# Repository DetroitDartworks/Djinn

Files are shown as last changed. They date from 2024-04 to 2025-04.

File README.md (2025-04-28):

*     05/22/24 - Updated Brushless Noidcore file(s) to fix some issues
*     06/13/24 - Added new Buttplate v2, Added new thumbhole stock extenders (must use Buttplate v1 with the extenders)
*     07/18/24 - Uploaded updated base flywheels (DDW Xing2 1404) AND new high concavity "Djinnshee" wheels for the Xing2 1404 motors
*     10/11/24 - Uploaded BETA Gonk-style PCAR insert for use with Djinnshee wheels, faux insert, and extended flycore dart guide
*     04/28/25 - Added new Board Box v2 that reinforces the upper portion of the Board Box for better retention. This can also still be used if the retention tab on the Lower breaks off

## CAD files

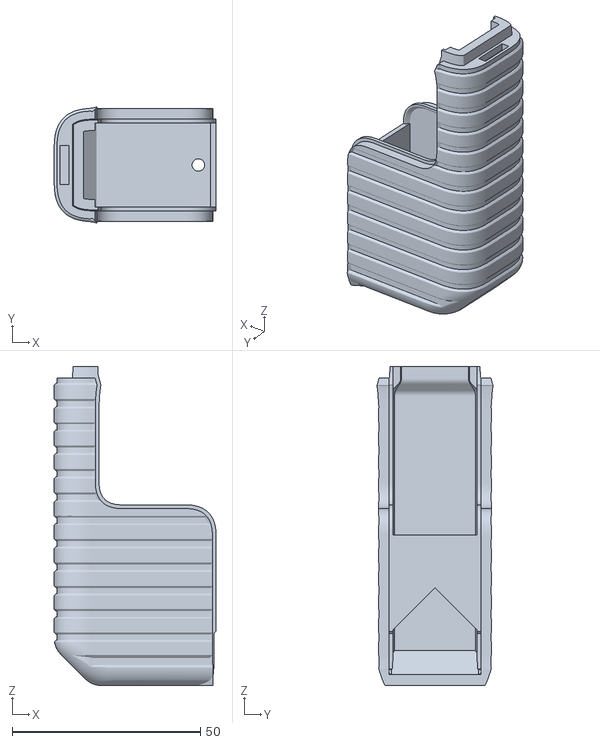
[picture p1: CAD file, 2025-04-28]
DDW Djinn - Board Box v2/DDW Djinn - Board Box v2.stl
42.9 x 30.9 x 84.6

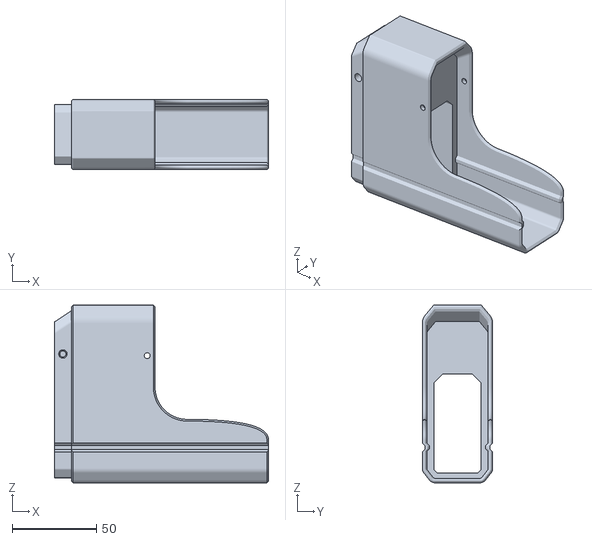
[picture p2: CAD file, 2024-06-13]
DDW Djinn Thumbhole Stock Extenders/DDW DJINN - Thumbhole Extender 50mm.stl
127.0 x 41.8 x 105.5

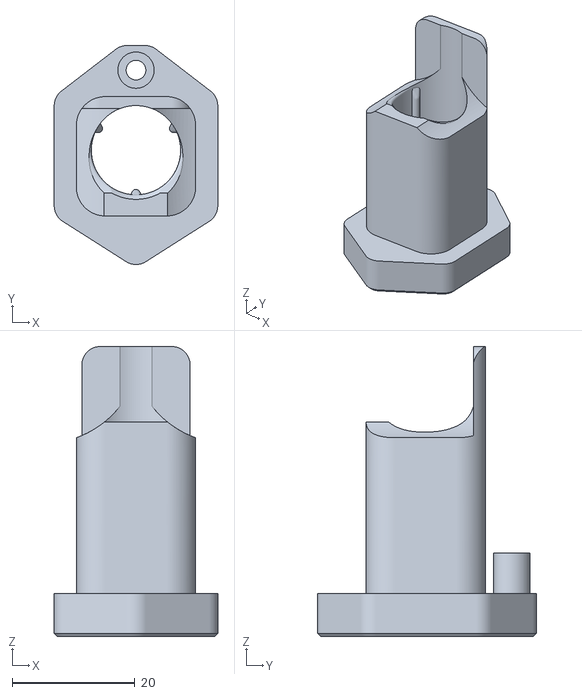
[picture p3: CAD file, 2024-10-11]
DDW Djinnshee Gonk PCAR Insert v3/DDW Djinnshee Gonk PCAR Insert v3.stl
26.6 x 35.6 x 47.2

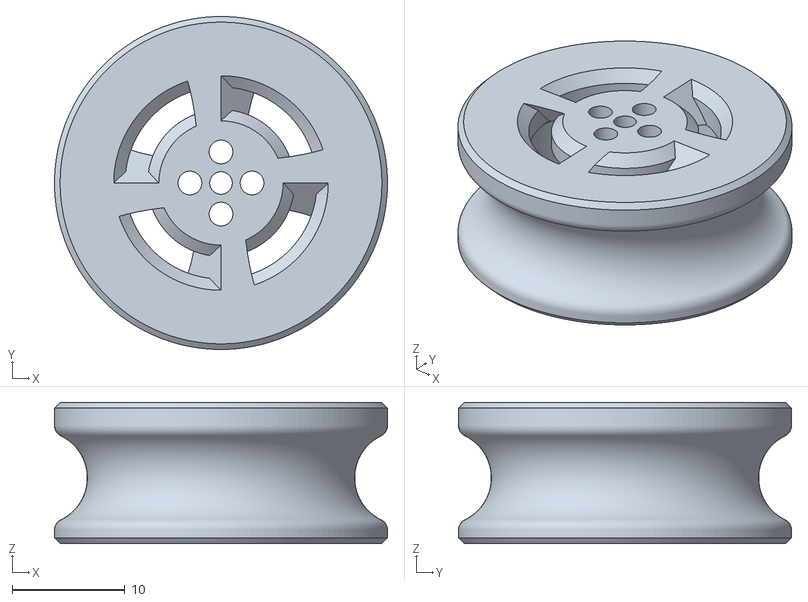
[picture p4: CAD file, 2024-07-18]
DDW Djinnshee Xing2 1404 Wheels/DDW Djinnshee Wheels Xing2 1404 v1 Mirror.stl
29.5 x 29.5 x 12.5

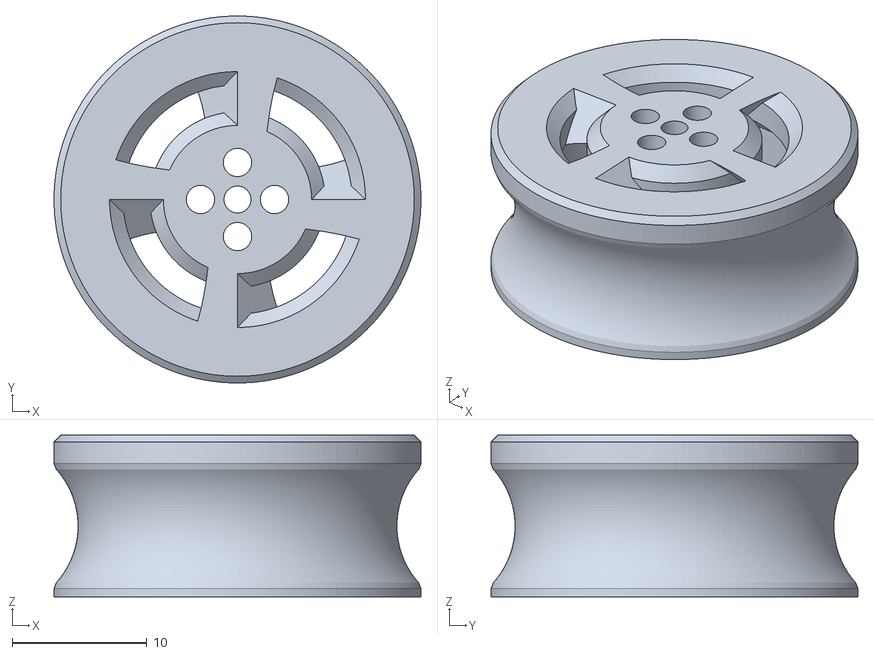
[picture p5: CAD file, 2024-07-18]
DDW Xing2 1404 Wheels and Dart Guide/Xing2 1404 DDW Wheel v4 Mirror.stl
27.2 x 27.2 x 12.0

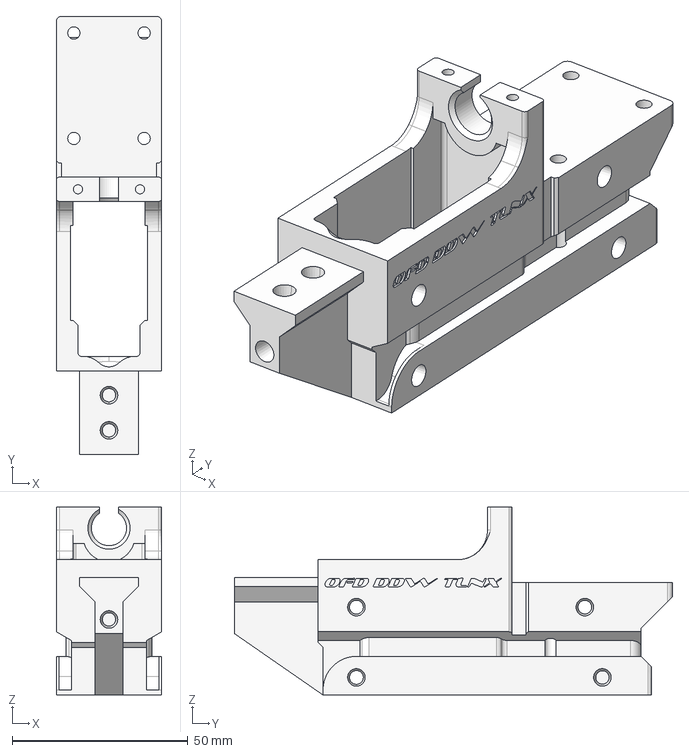
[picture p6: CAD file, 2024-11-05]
OFD-DDW-TLNX - BL NOIDCORE V2/OFD-DDW-TLNX BL NOIDCORE V2.step
30.0 x 124.8 x 53.5 mm

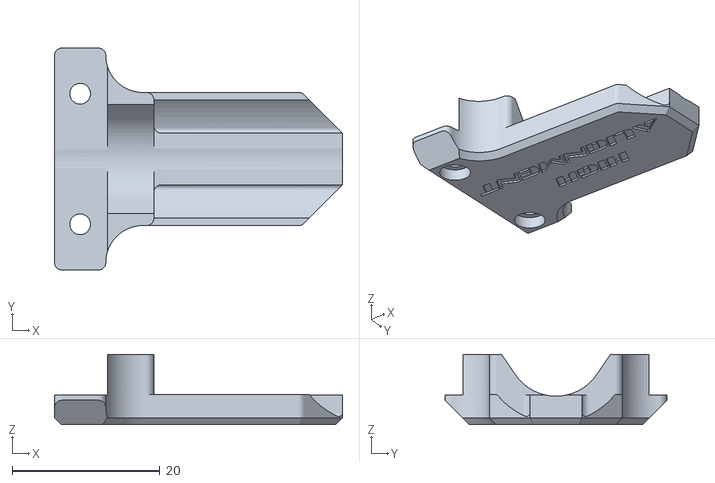
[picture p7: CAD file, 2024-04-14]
TalonaxeArmory_DDW_OFD_Modular_Brushless_Flycore/Dart Guides/NOIDCORE_Pusher_Guide_High_Straight_V1.STL
38.9 x 30.0 x 9.50

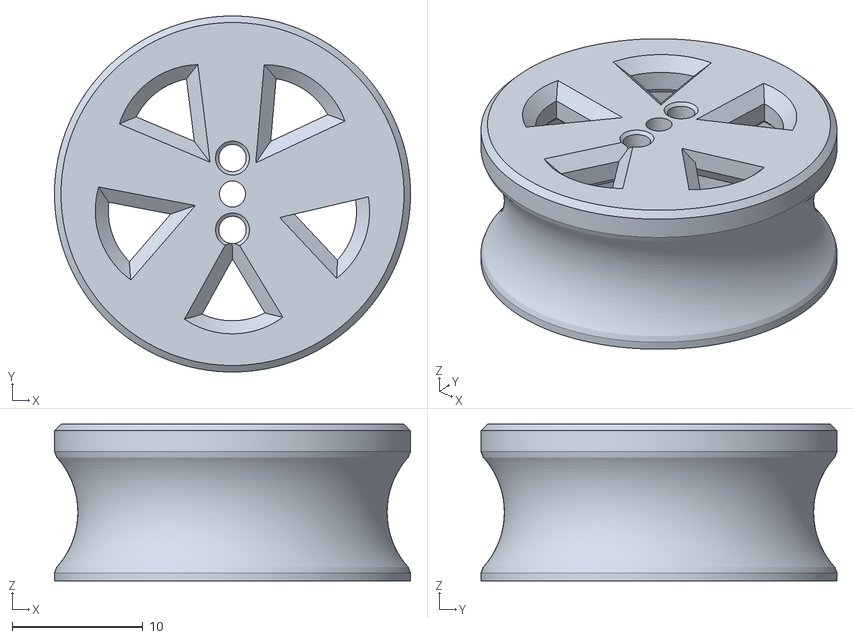
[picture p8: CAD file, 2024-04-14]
TalonaxeArmory_DDW_OFD_Modular_Brushless_Flycore/Flywheels/Xing2_1404Flywheel_v11.stl
27.2 x 27.2 x 12.0

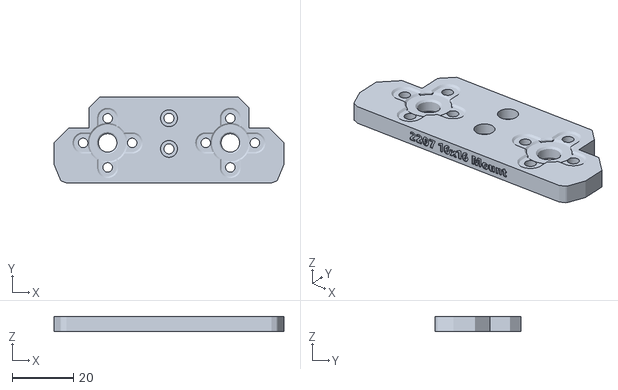
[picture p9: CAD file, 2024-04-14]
TalonaxeArmory_DDW_OFD_Modular_Brushless_Flycore/Motor Trays/2207Motors-40mmCrush-1616Mount_v2.stl
75.0 x 28.1 x 5.00

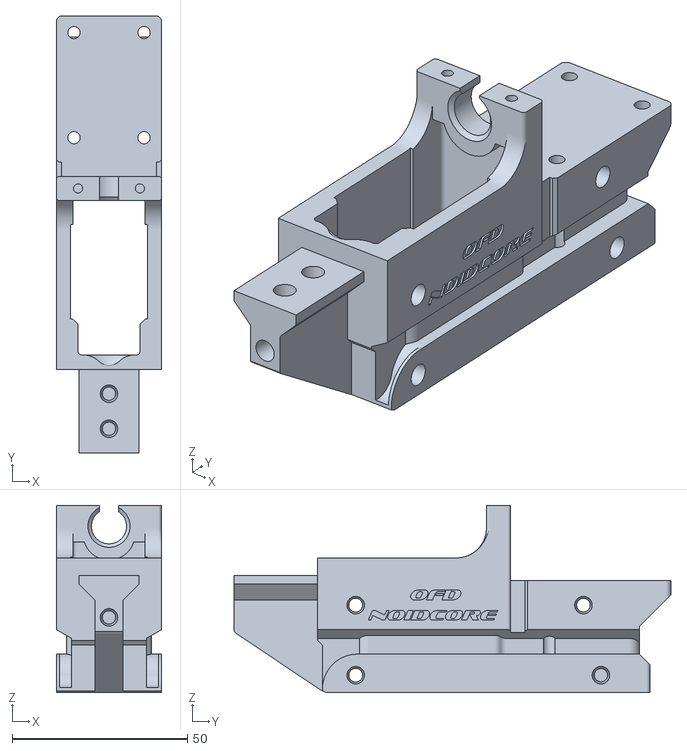
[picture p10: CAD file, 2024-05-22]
TalonaxeArmory_DDW_OFD_Modular_Brushless_Flycore/Talonaxe_DDW_OFD_Modular_Brushless_Flycore v12.stl
30.0 x 124.8 x 53.5

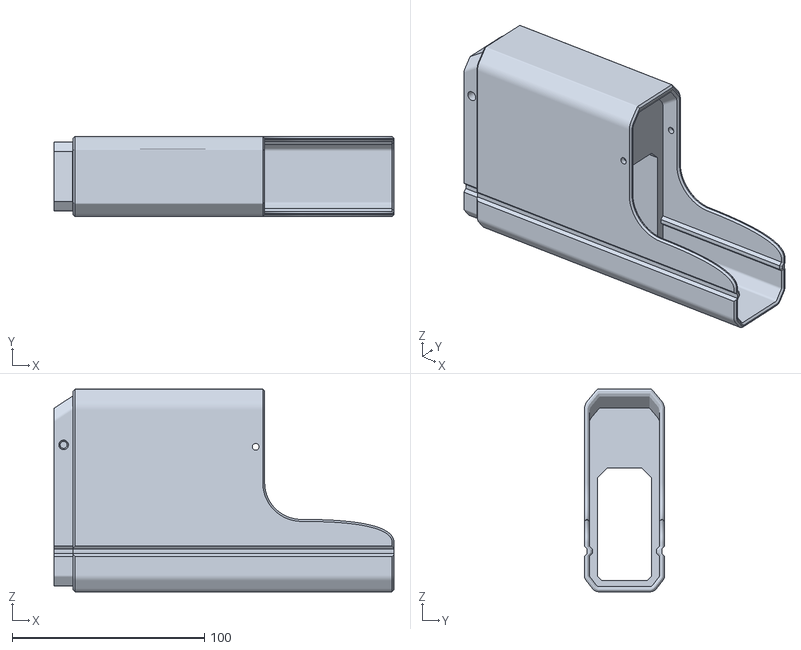
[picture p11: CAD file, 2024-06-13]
DDW Djinn Thumbhole Stock Extenders/DDW DJINN - Thumbhole Extender 100mm.stl
177.0 x 41.8 x 105.5

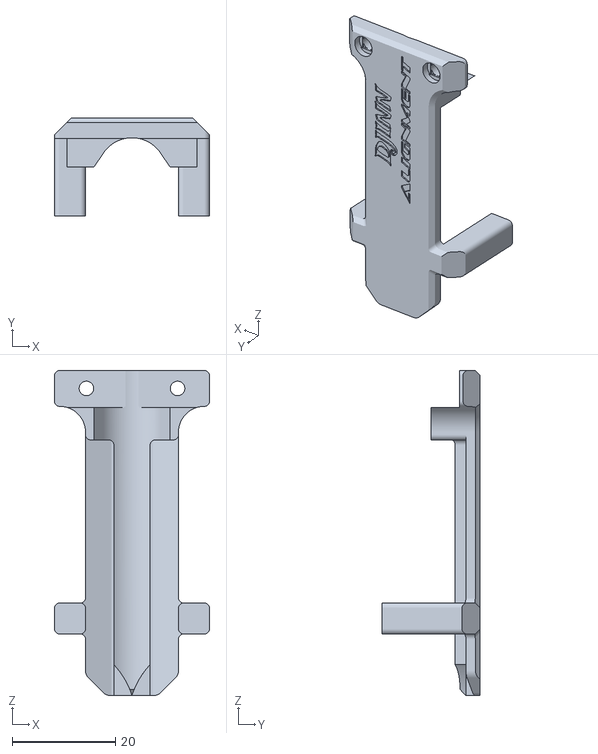
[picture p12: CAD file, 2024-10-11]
DDW Djinnshee Gonk PCAR Insert v3/Djinnshee Extended Pusher Guide.stl
30.0 x 19.0 x 62.9

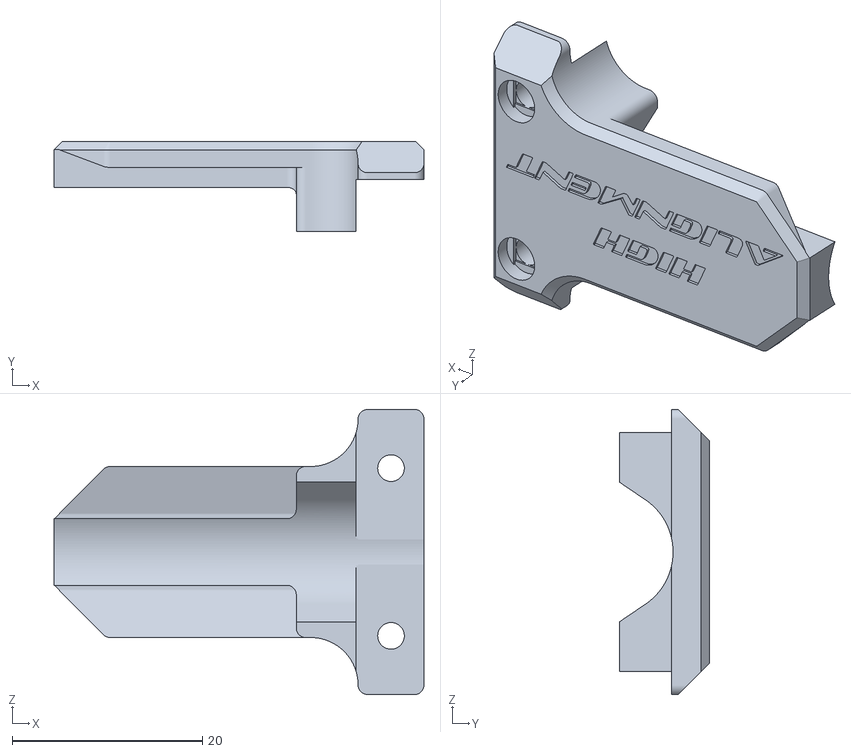
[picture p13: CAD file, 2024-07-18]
DDW Xing2 1404 Wheels and Dart Guide/Djinn Dart Guide.stl
38.9 x 9.50 x 30.0

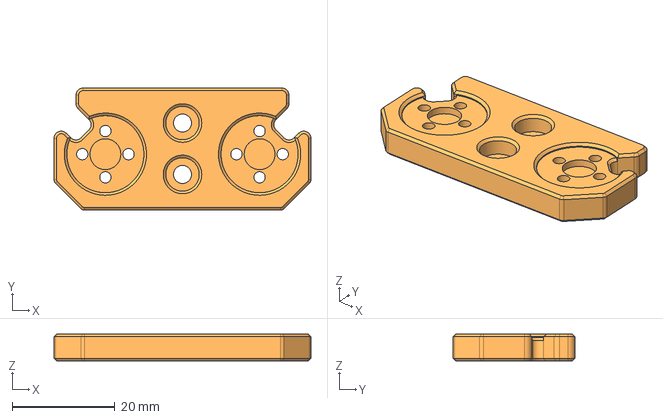
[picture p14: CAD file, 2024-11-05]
OFD-DDW-TLNX - BL NOIDCORE V2/MOTOR TRAY - OFD-DDW-TLNX BL NOIDCORE V2 - 30mm Xing2 1404.step
50.0 x 23.7 x 5.20 mm

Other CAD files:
DDW Djinnshee Xing2 1404 Wheels/DDW Djinnshee Wheels Xing2 1404 v1.stl
TalonaxeArmory_DDW_OFD_Modular_Brushless_Flycore/Flywheels/Xing2 1404 Flywheel-Vented.step
TalonaxeArmory_DDW_OFD_Modular_Brushless_Flycore/Motor Trays/1404Motors-30mmCrush-0909Mount_v2.stl
DDW Djinn Thumbhole Stock Extenders/DDW DJINN - Thumbhole Extender 75mm.stl
DDW Djinn Thumbhole Stock Extenders/DDW DJINN - Thumbhole Extender 25mm.stl
DDW Djinnshee Gonk PCAR Insert v3/DDW Djinnshee Faux PCAR Insert.stl
DDW Xing2 1404 Wheels and Dart Guide/Xing2 1404 DDW Wheel v4.stl
OFD-DDW-TLNX - BL NOIDCORE V2/Kodachi NOIDCORE_Pusher_Guide_High_Straight_V1.stl
OFD-DDW-TLNX - BL NOIDCORE V2/Kodachi NOIDCORE_Pusher_Guide_Low_Straight_V1.stl
OFD-DDW-TLNX - BL NOIDCORE V2/MOTOR TRAY - OFD-DDW-TLNX BL NOIDCORE V2 - 30mm Xing2 1404.stl
OFD-DDW-TLNX - BL NOIDCORE V2/OFD-DDW-TLNX BL NOIDCORE V2.stl
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

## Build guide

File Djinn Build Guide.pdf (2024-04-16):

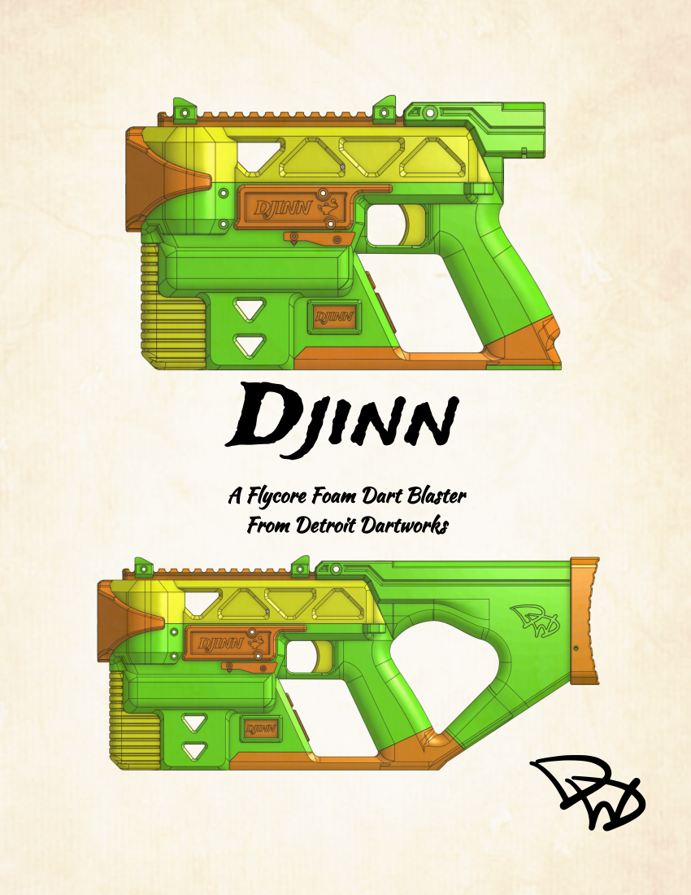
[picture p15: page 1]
Djinn

A Flycore Foam Dart Blaster
From Detroit Dartworks

NOTE: This is a FLYCORE blaster. You will need to download, print, assemble, and wire the proper Flycore files from OldFusionDesigns to complete this blaster.

Compatible Flycores
Any* straight talon Flycore or straight talon Noidcore Brushless OR Brushed

*As of 02-23-24

Required Hardware (NOT INCLUDING FLYCORE HARDWARE)
- 10-12 Heatset Inserts (same kind as used in the Flycore) (11 or 12 if using Thumbhole Stock)
- M3 x 8mm (7-16) - Amount depends on options. See below.
- M3 x 8mm Thumbscrew (1) (for battery door or Thumbhole Stock Buttplate)
- Standard nerf toy screws (10mm) (4-6) (4 for mag release & 2 for screen bracket)

Additional Optional Hardware
- M3 x 10mm (2 per individual sideplate, replaces 2 m3x8mm screws)
- M3 x 16mm (2 per individual fidlock panel, replaces 2 m3x8mm screws)
- M3 x 25mm (2 for ironsights, 2 per fidlock panel, 1 for n-strike stock attachment/Thumbhole Stock (replaces 1 m3x8mm))
- M5 x 30mm & m5 hex nut (1 for n-strike stock attachment/Thumbhole Stock)

Brushless Build Electronics
- Brushless Flycore - (See Talonaxe Brushless Flycore BoM for recommended Components)
- Neutron Solenoid (recommend getting the stronger spring)
- Omron style 15/21 amp microswitch (without lever)

Brushed Build Electronics
- Straight Talon Flycore (n20 or solenoid) (including optional cycle control switch for n20)
- Omron style 15/21 amp microswitch (without lever)
- Cherry db2 style 5/10 amp microswitch (without lever)

## Installation

Step 1: Wire & Assemble your Flycore
Wire up the Flycore outside of the blaster, using the printed parts to get a sense of wire lengths. There should be plenty of room inside the blaster so err on the side of too much wire as opposed to too little since some of the wires need to run longer.
Measure out your wire runs:
- Board sits underneath motors in the Board Bay.
- ESCs should be tucked into the motor well underneath the motors.
- Run XT30 through one of the wire channels, through the electronics bay behind the magwell, and through the Battery Door channel into the grip where the lipo will go.
- Run wires for screen and encoder through the other channel into the electronics bay behind the magwell.
- Run solenoid wires and trigger switch wires along each side of the flycore¹
- Keep in mind that if you install an on/off switch the wires need to go through the rectangular hole inside the handguard so the switch can be soldered and installed.
Step 2: Heatset Inserts
Install heatset inserts in the following locations:
- Lower - 2 in the front for the Muzzle, 1 in the rear of the top for the Upper, 1 in the bottom of the Grip for the Grip Connector, and 1 in front of the magwell for the Board Bay.
- Upper - 1 in the front for the Muzzle, and 3 along the top for the Picatinny Top Rail
- Battery Door: 1 in the battery door
- Thumbhole Stock Top: 1 (or both) on either side of the rear of the Thumbhole stock to secure the Buttplate.
Step 3: Mag Release
Insert Mag Release R and L into the holes on their respective sides of the blaster. Use 4 toy screws to secure Mag Release together.

2

2 Use all 4 screws as they provide extra rigidity to prevent the mag release from flexing.

1
I removed the flycore channel columns to help with this. You just need to be sure wires aren’t pinched upon installation of the flycore.

Step 4a: Install Switch and Trigger into Triggerpack (BRUSHLESS)
Place the microswitch into the recess with the button facing the trigger. Place the trigger in front of it. Place the other side of the triggerpack in place and then insert the triggerpack into the Lower.
Step 4b: Install Switches and Trigger into Triggerpack (BRUSHED)
Insert a 5x25mm spring into the recess in the back of the trigger and seat it on the nub in the triggerpack. The 15/21 amp microswitch sits in the upper recess with its button facing away from the trigger while the 5/10amp microswitch button should be secured to the triggerpack with 2 toy screws (from the outside of the triggerpack) with the button facing towards the trigger.
Step 5: Guts
Insert the board into the front compartment, run the wires as covered in Step 1. Set the ESCs above the board under each respective motor, and place the flycore into the blaster (you may need to depress the mag release or place the core slightly to the rear of the release and slide it forward into place). Once the core is in place, use 8 m3x8 screws to secure the flycore.
Step 6: Install Electronics in the Electronics Bay
I recommend installing the encoder knob first. I secure it in place with 2 6mm nuts (I 3d printed mine), one on the inside as a spacer and one on the outside to clamp it. Then insert the knob cover.
Put the power switch into place, making sure the lipo leads have enough length to reach comfortably through the battery door channel and into the grip. Last, slip the screen into its slot and secure it with the Screen Bracket and 2 toy screws.
Step 7: Secure the Board Bay
Once all peripheral electronics are installed and everything is plugged in properly to the board, slip the board into the Board Box Foregrip and slip it into place on the blaster, being sure not to pinch any wires. Secure the Board Bay Foregrip via the plastic tab at the top and an m3x8mm screw at the bottom.
Step 8: Attach Upper
Place the upper on top of the lower. Be careful not to pinch the solenoid or switch wires. Use a single m3x8mm screw to secure the back of the Upper in the rear screw hole. (If using the N-Strike stock adapter or the Thumbhole Stock, substitute an m3x25mm screw and attach the Nstrike adapter or Thumbhole Stock Top before attaching the Upper and Lower.

Step 9: Attach muzzle
Slide the muzzle down over the front of the Upper and use 3 m3x8mm screws to secure it to both the Upper and Lower.
Step 10: Attach Rail
If using the Upper Rail and Top Picatinny, use 3 m3x8mm screws in the 3 holes on the picatinny rail to secure it in place. Be sure to orient the rail correctly so that the holes line up (the middle hole is not centered on the length of the rail).
Step 11: Grip Connector & Battery Door
Ensure your power leads are plugged in inside the electronics bay and few through the Grip Connector. Set the front of the Grip Connector on the notch behind the magwell and then put it into place.Secure it with an m3x8mm screw.
Place the Battery door and secure it with an m3x8mm thumbscrew.
Step 12: Pew Pew Pew!

Installation of Optional Parts (continued on next page)

N-Strike Stock Adapter:
Remove the m3x8mm screw at the rear of the Upper. Slide the N-Strike Stock Adapter over the rear of the picatinny rail. Secure the N-Strike Stock Adapter with a m5x30mm screw and hex nut through the Picatinny Rail, and replace the removed m3x8mm screw in the rear of the Upper with an m3x25mm screw through the N-Strike Stock Adapter and Upper, into the Lower.

Thumbhole Stock:
Remove the m3x8mm screw at the rear of the Upper. Replace the Grip Connector & Battery Door with the Thumbhole Stock Bottom. Route the wires for the battery from the electronics bay through the Thumbhole Stock Bottom and Top. Slide the Thumbhole Stock Top into position on both the Thumbhole Stock Lower (being sure not to pinch the wires) and onto the rear of the blaster and picatinny rail.
Use a m3x8mm screw to secure the Thumbhole Stock Bottom to the grip of the Lower. (Be careful as the wires for the battery run through this channel, so be sure they are to the side of your screwdriver.)
Secure the Thumbole Stock Top using a m5x30mm screw and hex nut through the picatinny rail and an m3x25mm screw through the Top, Upper, and into the Lower. Attach the Thumbhole Stock Buttplate to cap the battery compartment with an m3x8mm thumb screw.

Iron Sights:
Attach the Front and Rear Iron Sights with 2 Iron Sight Clamps and 2 m3x25mm screws and hex nuts to the picatinny rail.

Electronics Inserts:
Encoder Knob Insert: Use in conjunction with either the Encoder Nut (if you still want a power switch) or the Power Switch Insert. Encoder Knob insert threads into either part, leaving the triangle on the outside of the shell.
Power Switch Insert: Use in conjunction with the Encoder Knob insert for brushed builds with no power switch. Insert the Power Switch Insert from the inside and secure it in position with the Encoder Knob insert (from the outside)
Screen Inserts: Replaces the microviewer screen. Retain with the screen bracket used for the screen.
Slim Power Switch Insert: Used for the slim style power switches. Press fit the slim power switch into the flared side of the insert, then press fit the insert and switch into the Lower from the outside.

Side Plates:
Replace the 2 rear m3x8mm screws retaining the flycore with m3x10mm screws through the Side Plate.

Fidlocks:
Install the medium fidlocks into the threaded holes in the Fidlock panel before installing the panel onto the blaster. Replace all 4 m3x8mm screws on whichever side you want to mount the fidlocks that are retaining the flycore with m3x25 in the front holes and m3x16 in the rear holes through the Fidlock panel.

Encoder Locks:
These are installed to create a “Tournament Lock” solution. Which prevents the encoder knob from rotating (no scrolling in the menu or adjusting power levels on the fly) while still allowing it to be “clicked” to switch between firing modes. To install, remove the Encoder Knob cover, slide the Encoder Lock Cover over the encoder shaft and tighten down onto the threaded portion of the encoder shaft to the point that the captive button is flush against the encoder shaft but not depressing it.

## Printing Guide

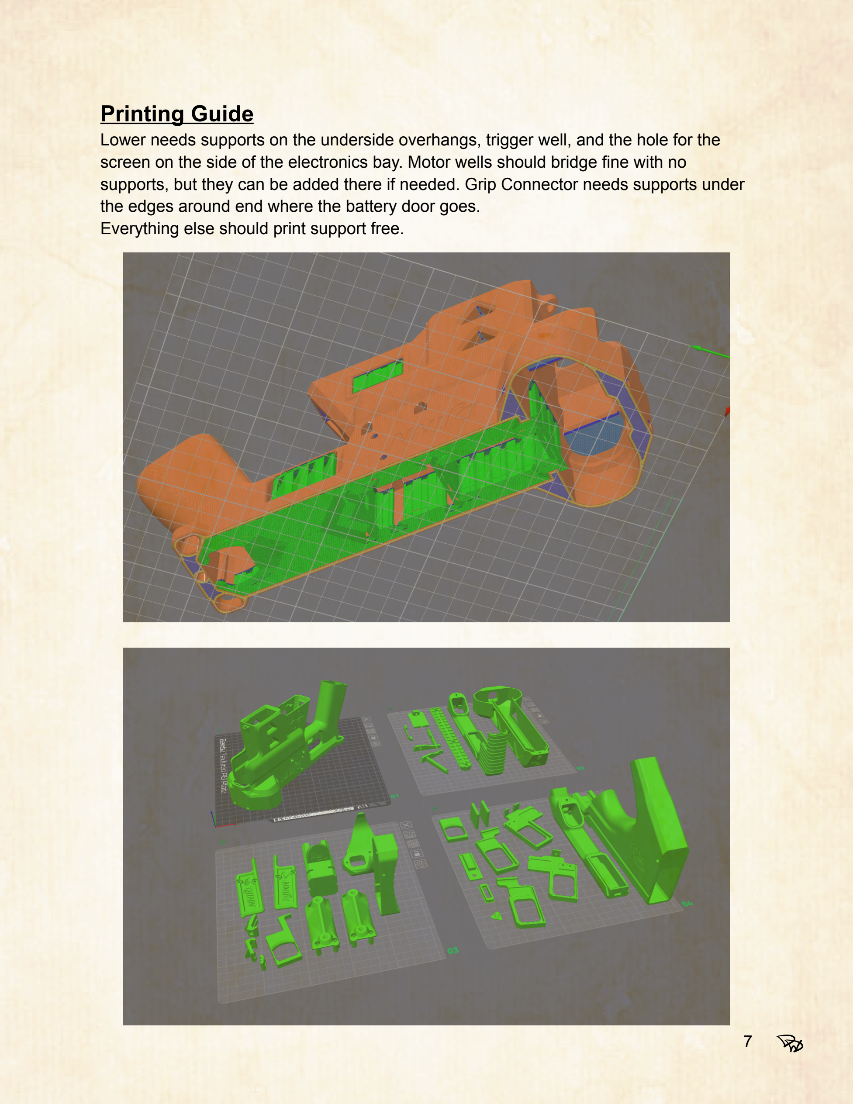
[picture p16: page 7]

Lower needs supports on the underside overhangs, trigger well, and the hole for the screen on the side of the electronics bay. Motor wells should bridge fine with no supports, but they can be added there if needed. Grip Connector needs supports under the edges around end where the battery door goes.
Everything else should print support free.

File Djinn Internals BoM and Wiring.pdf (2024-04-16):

# Brushless Flycore Wiring Setup

# Bill of Materials

0.96" OLED - https://www.amazon.com/gp/product/B09C5K91H7/Rotary (chose one)
20mm Encorder: https://www.amazon.com/gp/product/B07DM2YMT4/15mm Encoder: https://www.amazon.com/dp/B07D3D64X7/
Trigger Switch: https://www.amazon.com/gp/product/B00MFRMFS6/
47UF Capacitor (if using the Mjolnir Board PCB): https://www.amazon.com/gp/product/B0BQ59XWNR/ref=ppx_yo_dt_b_search_asin_title?ie=UTF8&th=1
Currently used motors: iFlight Xing2 1404 4600KV https://www.racedayquads.com/products/iflight-xing2-1404-4600kv-micro-motor
ESC: any blheli32 ESCs (ones I use: https://www.racedayquads.com/products/spedix-gs35-35a-individual-esc-2-6s-dshot1200?variant=4258743123979 )
Arduino Nano3
Neutron Solenoid
1 Mjolnir Board

## Wire Lengths

Encoder Wires - 4x 8 inches 22g OLED Wires - 4x 8inches 22g Trigger Switch - 2x 12inch 22g Power (Pistol Mode) - 17in x2

# Overview

## Mjolnir PCB Setup

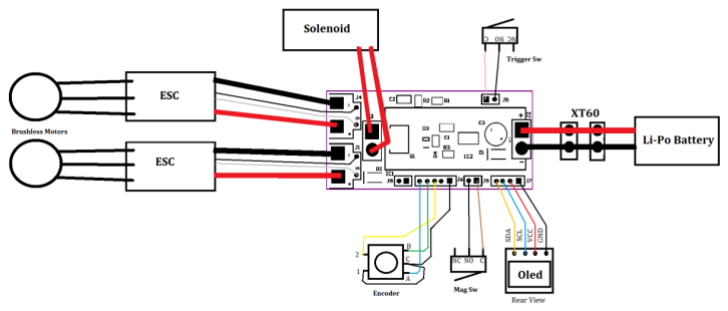
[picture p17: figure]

## Arduino is mounted with 15-pin break aways on PCB Trigger, Encoder, ESC Signal and 0.96” OLED utilizes JST-XH 2.56mm connectors with 22g wire Solenoid, Power and ESC Power uses XT-30 connectors with 20g wire

## KY-22 Rotary (without PCB) Encoder Diagram

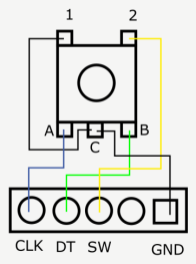
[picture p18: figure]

Encoder facing front
Ground Wire Connects to Tabs 1 and C SW Wire connects to Tab 2
DT Wire connects to Tab B
CLK Wire connects to Tab A

## O.96” OLED Screen

Wires from OLED screen connects to sections J7 (4 pin) of PCB. This Is the only 4-Pin JST Connector on the PCB.

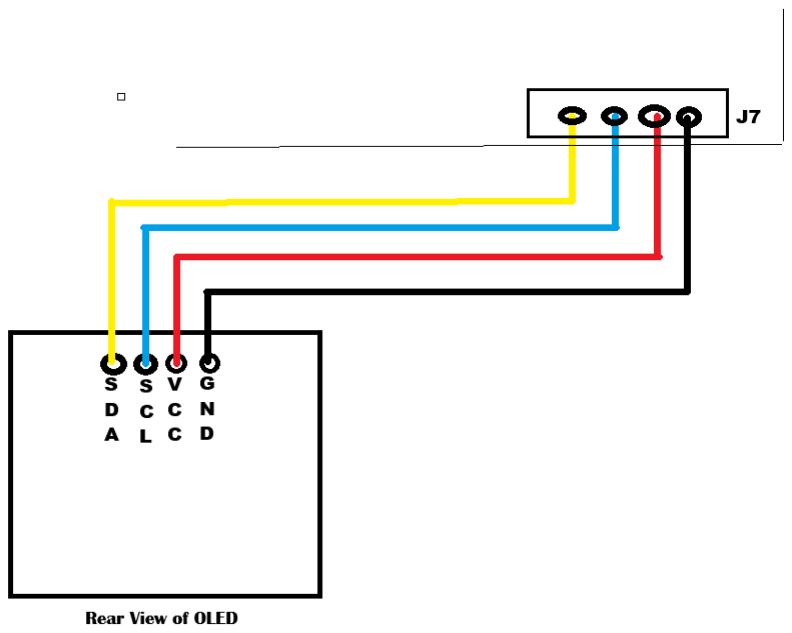
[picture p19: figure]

## Trigger

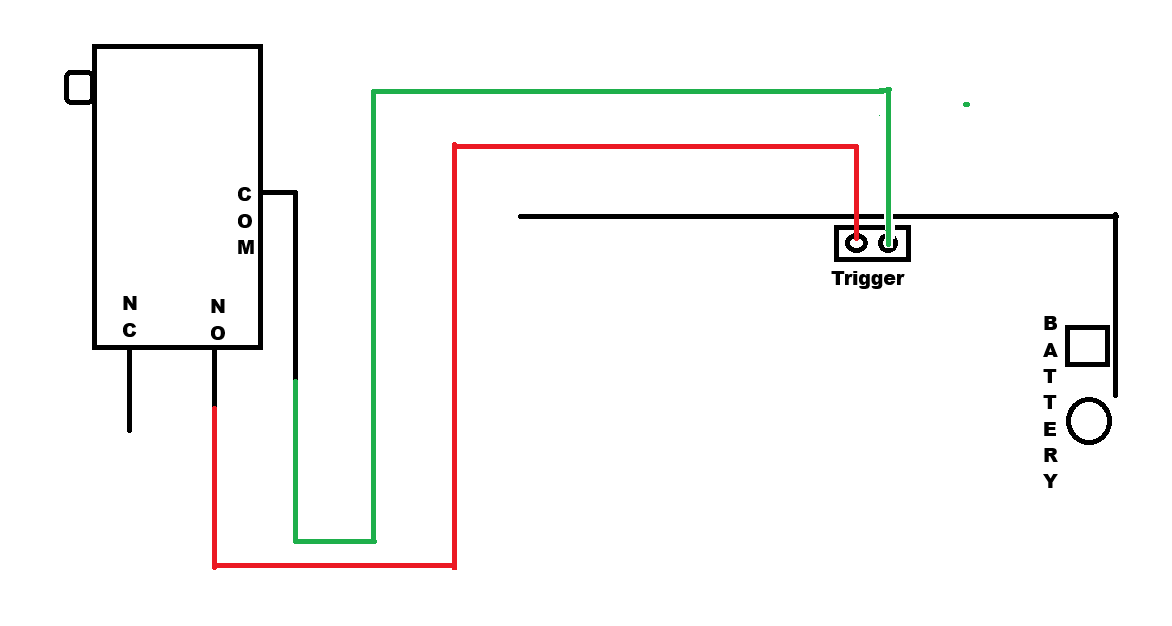
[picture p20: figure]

Wire from the NO (Normally Open) and Comm to the 2-pin Trigger port.

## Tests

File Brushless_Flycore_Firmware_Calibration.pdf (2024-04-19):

## Talonaxe Armory Brushless Flycore Firmware Instructions

1) Basic Operation

Once you have powered on the unit, it will play its start up tones along with the Djinn Logo on the OLED, followed by a confirmation tone signaling the system is ready to fire, and the Home Screen on the OLED.

The Home Screen has most information needed for safe operation of the blaster.

OLED - Home Screen:
1st Line: Top Left - Bat volts: 11.4v, Top Right - Game Timer
2nd Line: Select fire mode: Single / Burst: X / Full Auto
3rd Line: ROF: MAX
4th Line: Pwr: 50% (Power to the ESCs)
Ammo Counter (Large Digit) (disabled in configuration menu by default)

Please note that ROF and Pwr can change relative to your select fire mode and your profile settings within the configuration menu.

Select Fire
This kit includes 3 fire modes, Single Fire, Configurable Burst and Full Auto.
To cycle the Select Fire Modes, quickly press and release on the encoder (Short Press). You can see which fire mode you are in by looking at the 3rd Line of the Home Screen which will read Single / Burst 3 / Auto
The Burst Fire is set to 3 Rounds by default, but can be changed in the System menu.

Rate of Fire (ROF)
ROF is set to Max by default. You may change this in the configuration menu depending on which fire mode you are in. See the table below

Configuration Menu
The Configuration Menu gives you access to almost all of the settings for the firmware. You can make any changes you wish to your profile, to experiment with what works best for you. If you make a change which you cannot recover from, you may reload the Default Profile.

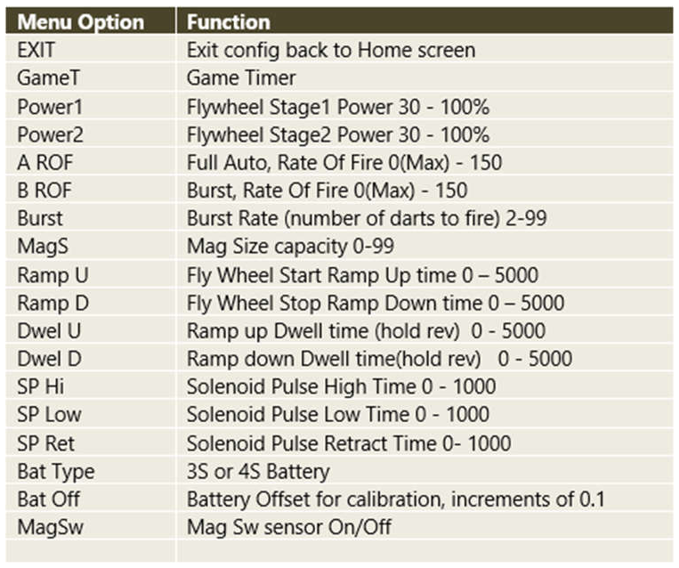
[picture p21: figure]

Power2 – Only matters if you have a dual-stage motor setup. This number can never be lower
than | Power1.

Game Timer - This is an operator preset countdown timer, representing the game mode time to be played. Set in minutes. E.g. 00:20 = 20 minute Game Time. On exit from Config screen, if this is not at zero, timer will start counting down from value set. At 1 minute from timer expiry, screen will flash, to indicate end of game coming in less than a minute.

Bat Type – Default set to 3S. While the system is capable of 4S, only select it if you have a 4S battery installed, as this matters for Voltage Protection and Low Power Cuto.
Bat O – a Battery Oset to correct for any errors in the OLED reading compared to a voltmeter. Can be adjusted in .1v increments.

MagSw – Turns o or on the Mag Switch detection. O by default as the Djinn doesn’t use a Mag Switch. Disables the Ammo Counter and “Mag Dropped” display”

Restoring Default Profile
To load the default profile and restore the unit to Factory Settings, simply hold the trigger while powering up the unit, and releasing when the OLED informs you to do so.

## Solenoid Calibration

The kit comes pre-flashed with settings that the development team has found works best for their setup using the OutofDarts Neutron High Rate of Fire (double spring) Solenoid on a Tattu R-line 750 3S battery.
If you use a dierent battery, or swap to 4S, then you will have to recalibrate your solenoid for better ROF and performance.

In order to calibrate your solenoid, you will need to edit the following Lines:

SP Hi (Solenoid Pulse on Time High)
SP Low (Solenoid Pulse on Time Low)
SP Ret (Solenoid Pulse Retract Time)
For the first step, we want to focus on the Retraction Rate (SP Ret) SP Ret Calibration:
1. Fully Charge your battery
2. Set the fire rate to Auto
3. Start with SP Ret 100 (Pulse Retract time 100ms) to see if the Solenoid is fully retracting between shots. Use your finger to feel for the retract if nessacary
4. Adjust SP Ret up or down as needed, until you have a consistent and reliable retraction. Because Solenoids will retract slower with a full magazine, add approx. 10ms to this number.
After you have completed the SP Ret calibration, you can then move onto your Pulse time (SP Hi, SP Lo)

SP Hi and SP Lo Calibration
1. Fully Charge battery
2. Adjust SP Hi and SP Lo to 150ms
3. Slowly lower each setting (keeping them the same) until the strokes are quick, but not short stroking the solenoid (extending the solenoid before full retraction).
4. Use your finger to gauge how hard the solenoid is hitting it
5. Keep reducing the time until it starts to feel weaker
6. Add a small amount of (5-10ms) as a safety margin.
7. Test the firing rate. Write this value down for future reference. (SPHi)
8. Bring the Battery to Storage charge. Then repeat steps 3 – 7 for SP Lo, adjusting up or down as needed.

Once you have set up your Retraction and Pulse Times for your solenoid, make sure to write these values down in case you ever have to change them, or reset to factory settings. Reducing these values will make the solenoid fire faster, but at the cost of reliability.

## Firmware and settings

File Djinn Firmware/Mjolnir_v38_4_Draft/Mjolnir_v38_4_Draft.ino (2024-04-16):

#include <EEPROM.h>
#include <SSD1306AsciiWire.h>
#include <Wire.h>

#include "MenuHelpers.h"
#include "Logo.h"
#include "History.h"

#define VERSION 38
/* 10-12-23
  For the Nerf Comunity, open progect... RICHARD NICHOLSON from NEW ZEALAND

  Brushless | Solenoid Pusher | Singal Trigger | Mag Detetor Sw | 3 Pos Select Fire Sw | I2C OLED 128 x 64 display | Rotary Encoder with PB_Switch | Serial DeBUG 115200 Buad

  -------------------------------------------------------------------
    *** Mjolnir V1 Hardware Pin out. This is the Default setting
  -------------------------------------------------------------------
  *Nano PCB layout, USB pointing Up
 PIN |  Real would connection |  In/Out    | Register

  
  RHS
  D12     - Encoder SW             => Input        PB4           //  - Could use a PB = Single, Burst,Full Auto, Single, Burst,Full Auto...
  D11     - Mag Sensor             => Input        PB3   OC2A    //  - NO to D11 and COM to GND
  D10     - ESC stage 1 signal     => Output       PB2   OC1B    //  - 2 x ESC go on this signal 1st stage
  D9      - ESC stage 2 signal     => Output       PB1   OC1A    //  - 2nd Stage
  D8      - Selectfire Sw In1      => Input        PB0   *NEW    //  - Slide switch pin for Select fire
  D7      -                        => Input        PD7           //  -
  D6      -                        => Output       PD6           //  -  - OC0A
  D5      - Solenoide Pusher       => Output       PD5           //  - Mosfet Trigger
  D4      -                        => Output       PD4           //  -
  D3      - Input - Encoder DT     => Input        PD3   /Int1   //
  D2      - Input - Encoder CLK    => Input        PD2   /Int0   //

  LHS
  D13     - Tracer Darts Led       => Output       PB5  *NEW     //  - Use PCB led as indicator for testing.   *** Compile Time option
  A0/D14  - Rev Sw                 => Input        PC0  *NEW     //  - NO to A0/D14 and COM to GND             *** Compile Time option
  A1/D15  - Solenoid Stop          => Input        PC1           //  - Narfduino: Output - Solenoid Stop, left for compatablity with Narfduano PCB   *** Compile Time option
  A2/D16  - Trigger                => Input        PC2           //  - NO to A2/D16 and COM to GND.
  A3/D17  - SelectFire Sw In2      => Input        PC3  *NEW     //  - Slide switch pin for Select fire
  A4/D18  - OLED display  SDA      => I2C          PC4           //  -
  A5/D19  - OLED display  SCL      => I2C          PC5           //  -
  A6      - Analog Input Not used  => Input        ADC6          //  - ADC input only, no digital code, programing functions on this pin
  A7      - Analog Battery Reading => Input        ADC7          //  - Resistor devideder 47K/10K

  -------------------------------------------------------------------
            Mjolnir V2 Hardware Pin out. V2 pinout can be selected via compile time switch
  -------------------------------------------------------------------
  Nano PCB layout, USB pointing Up
  RHS PIN |  Real would connection |  In/Out    | Register

  D12     - Encoder SW             => Input        PB4           //  - Could use a PB Single, Burst,Full Auto, Single, Burst,Full Auto...
  D11     - Mag Sensor             => Input        PB3   OC2A    //  - NO to D11 and COM to GND
  D10     - ESC stage 1 signal     => Output       PB2   OC1B    //  - 2 x ESC go on this signal
  D9      - ESC stage 2 signal     => Output       PB1   OC1A    //  -
  D8      -                        => Output       PB0           //  -
  D7      - Encoder DT             => Input        PD7           //  -
  D6      -                        => Output       PD6   OC0A    //  -
  D5      - Solenoide Pusher       => Output       PD5           //  - Mosfet Trigger
  D4      -                        => Output       PD4           //  -
  D3      - SelectFire Sw In2      => Input        PD3   /Int1   //  *** Compile Time option
  D2      - Selectfire Sw In1      => Input        PD2   /Int0   //  *** Compile Time option

  LHS
  D13     - Tracer Darts Led       => Output       PB5           //  - Use PCB led as indicator for testing.   *** Compile Time option
  A0/D14  - Rev Sw                 => Input        PC0           //  - NO to A0/D14 and COM to GND             *** Compile Time option
  A1/D15  - Solenoid Stop          => Input        PC1           //  - Narfduino: Output - Solenoid Stop, left for compatablity with Narfduano PCB   *** Compile Time option
  A2/D16  - Trigger                => Input        PC2           //  - NO to A2/D16 and COM to GND.
  A3/D17  - Encoder CLK            => Input        PC3           //  -
  A4/D18  - OLED display  SDA      => I2C          PC4           //  -
  A5/D19  - OLED display  SCL      => I2C          PC5           //  -
  A6      - Analog Input Not used  => Input        ADC6          //  - ADC input only, no digital code, programing functions on this pin
  A7      - Analog Battery Reading => Input        ADC7          //  - Resistor devideder 47K/10K


  ---------------------------------------------------------------------------------------------------------------------------------
   Hardware
     - SSD1306 128 x 64 OLED Display NOTE: OLED_ADDR may need to be set correctly
     - Rotary Encoder with inbuilt PB Switch. DT to outside pin, CLK to oustide, GND to middel pin
     - Battery Resistor Devider on A7 47k/10K, with a bat, else code will say low bat
  ---------------------------------------------------------------------------------------------------------------------------------
READ.ME            **** V34 code and hardware changes ****
    
  This code suports a number of new features
    Optional Sliding Select Fire Switch
    Optional Rev switch, alwoing pre spin up to Ideal speed as set in the menu
    Optional Tracer Dart Output
    Simple Firmware configuration via editing compile time switchs, and default menu values, that are used in the Oled menu
    Default Menu values and compile time switchs located at start of file for easy editting
    
    Simpl Blaster configuration. Trigger and select fire switch only, set default values before firmware download
    to
    All Features:Oled, Encoder, Select Fire, Mag Sw, Rev Sw

    Idel Mode for flywheels, can set the ideal value in Menu. Turn on and off via Long trigger press (2 seconds) or use Rev Sw
    
  Hardware:
  Both V1 and V2 Mjolnir PCB wiring is suported via compile time code switchs. The Default is V1 hardware (V2 underdevelopment).
  
  New Hardware features, use unused pins from V1 plateform. You will need to solder wires to the Nano Pins on underside of Mjolnir V1 PCB
    - D8 Select Fire slide Sw input 1
    - A3 Select Fire Slide Sw Input 2
    - A0 Rev Sw Input
    - D13 Tracer dart output
    
  Optional Tracer Darts output via D13 (on Board Led). Follows Rev. Requires a driver suggest use mosfet
  
  Optional 3 position, Select Fire switch - Via compile time code switch. Encoder Select fire PB does not work with this enabled
  
  Optional Rev Switch, Via compile time code switch.  Ideal speed value set in config menu
  
  Mag Switch On/Off know done via compile time code switch (saves on memory)
  
  Logo can be turned off to save 3% of memory for code space Via compile time code switch
  Dipaly Fip can be done Via compile time code switch

  you can find the compile time switches just below, after the comments
  --------------------------------------------------------------------------------------------------
  
  INSTRUCTIONS

  Copy the Four files:

     Mjolnir.ino
     History.h
     Logo.h
     MenuHelpers.h

  Into one folder, and initiate the Adrouno IDE by clicking Mjolnir_vnn.ino
  Under Tools set the Board Type:Arduino Nano, Processor:ATmega328P (old Bootloader), and Com port

  Verify program, top left.
  It may error, requiring libarie files. These can be found under Tools/Manager Libaries..

  Once it Verifies OK...
  Upload to Arduino ( the next button)
  If updoad fails try changinging the Processor under Tools/Processos, to ATmega328P

  Set Serial Monitor, to 11520 baud, for debug output. Not required. Will Display version Number

  First time upload will load default values into EEprom and configuration screen
  -----------------------------------------------------------------------------------------

  ROTARY ENCODER
  Use Rotary Encoder Push Button (PB), Short click to change Select Fire Mode. Mode is on default display (Single / Burst: 2 / Full Auto)
  Use a Long Click to get into the Configuration screen, short click to get out when on the EXIT tag. Menu goes around in circle.

  OLED DISPLAY - Default home Screen
  Bat volts: 11.4v
  00:00:00 Game timer HH:MM:SS, set in minutes via Config Menu
  Select fire mode: Single, Burst: 2, Full Auto (Use short clicks to change Select Fire Mode
  ROF: MAX, Rate Of Fire, default is max Pusher speed, ie changeing value, via config screen will slow it down
  Pwr: 50%, Flywheels output, default is on 50%, you can change the power in the config menu, it will go faster or slower
  Ammo Counter: reset via mag switch. no trap on zero count.
  Use short clicks to change Select Fire Mode (Single / Burst: 2 / Full Auto)
  Long Click to get into the Configuration screen, short click to get out when on the EXIT tag, top or bottom of menu

  OLED DISPLAY - Configuration Screen. Long Click to enter.
  To change values, Click to get # rotate to change value, click to accept. Values are saved to EEPROM instantly

  EXIT           // Exit config back to default run screen
  GameTm:        // Count Down, Game Time Set in Minutes. Starts when exit config it not zero
  Power1:        // Flywheel Stage1 Power 30 - 100% Default: %50
  Power2:        // Flywheel Stage2 Power 30 - 100% Default %50 NOTE: can not be set below Stage 1 power, will auto correct
  A ROF          // Full Auto, Rate Of Fire 0(Max) - 150 Default: Max
  B ROF          // Burst, Rate Of Fire 0(Max) - 150 Default: Max
  Burst          // Burst Rate (number of darts to fire) 2-99 Default: 2
  MagS           // Mag Size capacity 0-99 Default: 18
  Ramp U         // Fly Wheel Start Ramp Up time 0 - 5000 Default: 0 (Fastest)
  Ramp D         // Fly Wheel Stop Ramp Down time 0 - 5000 Default: 4000
  Dwel U         // Ramp up Dwell time 0 - 5000 Default: 0 Use this to hold the rev
  Dwel D         // Ramp down Dwell time 0 - 5000 Default: 200 Use this to hold the rev
  SP Hi          // Solenoid Pulse High Time 0 - 1000 Default: 35
  SP Low         // Solenoid Pulse Low Time 0 - 1000 Default: 45
  SP Ret         // Solenoid Pulse Retract Time 0- 1000 Default: 45
  Bat Type       // 3S or 4S default 3S
  IdleSpd        // Battery Offset for calibration, increments of 0.1 displayed as interger
  ROF_Tm         // Mag switch detect enable on/off
  EXIT           // Exit config back to default run screen

  To load factory default settings, Hold trigger ON during power up or reset, let go when screen says too.

  ---------------------------------------------------------
  SOLENOID TUNING : to get best ROF you need to do this
  ---------------------------------------------------------
      In order to get a good solenoid calibration/tune, you need to have 3 things:
      - Push-out Time when LiPO is fully charged, ~12.5v or similar on 3S
      - Push-out Time when LiPO is depleted, storage voltage 11.5v or similar on 3S
      - and Retract Time.

     It is advisable to disconnect the ESC signal wire so that you don't have the motors draining power, and affecting your tune.

     We need to change these values in the Config Screen
       SP Hi, Solenoid PulseOnTimeHigh, default = 35;
       SP Low, Solenoid PulseOnTimeLow, default = 45;
       SP Ret, Solenoid PulseRetractTime = 45;

     Focus on the return rate first
     Via config menu:-
       Change A ROF to Max, it is by default
       Change SP Hi, Solenoid Pulse On Time High = 150
       Change SP Low, Solenoid Pulse On Time Low = 150
       Change SP Ret, Solenoid Pulse Retract Time = 100
     Exit Config

     Set select fire to Full Auto
     Start with SP Ret, at 100ms,to see if the solenoid is fully retracting between shots. Else it will be short strocking
     You might be able to use your finger to feel it. Increase or reduce this number until you have a consistent and reliable retraction.
     n.b. solenoids will retract slower with a fully loaded magazine, so once you have found the number, add a bit extra to it (like 10ms)
     To attchive the above may require multi edits

     Then focus on the fully charged pulse time. Fully charge your LiPO. Start reducing both SP Hi and SP Low
     (keep the numbers the same) until it's quick, but not so quick as it's short-stroking.
     Use your finger up the magwell to determine how hard the solenoid is hitting it. Keep reducing the time until it starts to feel weaker,
     then back off.
     Add a bit extra to it for safety margin. Write down this value.

     For the low battery discharge time, bring the LiPO to storage charge. Then do the same thing as above.

     Once you have both the SP Hi and SP Low values, key them in and test the solenoid over a range of battery voltages.
     Reducing the timing will make it faster, at the expense of reliability.

     Neutron: Thous 3S: SP HI = 47, SP Low = 47, SP Ret = 27
     Neutron: Rich 3S 25C: SP HI = 38, SP Low = 42, SP Ret = 27
     Neutron: Rich 3S 25C RD With 28v boost : SP HI = 28, SP Low = 32, SP Ret = 14

     Big 35mm: Rich values 4S RD: SP HI = 23, Sp low = 30 SP Ret = 23
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
void loop() {
  
  
  ProcessDebouncing();              // Process the pin input, and handle any debouncing
  ProcessButtons();                 // Where interperation is necessary, handle it here Trigger is being done here
  ProcessBatteryMonitor();          // Check battery voltage occasionally
  ProcessMagRelease();              // Handle when a magazing is dropped out
  ProcessSystemMode();              // Find out what the system should be doing
  ProcessConsoleButtonManager();    // Work out what to do based on the console button input
  ProcessDisplay();                 // Update the Oled display

  if ( PrevCommandRev != CommandRev )     // Detected a change to the command. Reset the last speed change timer
  {
    TimeLastMotorSpeedChanged = millis();
    PrevCommandRev = CommandRev;
  }
  ProcessSpeedControl();            // Process speed control to resolve a % target
  ProcessMotorSpeed();              // Calculate the new motor speed in terms of a PWM signal
  ProcessMainMotors();              // Send the speed to the ESC

  ProcessFiringControl();           // Handle the cycle control here

  ProcessPusherControl();           // Handle the pusher management here
  ProcessGameTimer();               // update game timer

  //Debugging EEPROM write count
  //int writeCount = EEPROM.read (eepromWriteCountAddress);
  
/*
  Serial.println("AmmoCounter State");          //readout serial within main loop
  Serial.println(AmmoCounter);
  Serial.println("SystemMode");
  Serial.println(SystemMode);
  Serial.println("MagSwEnable");
  Serial.println(MagSwEnable);

*/
  
  if (Serial.available() > 0) {
    // Check for a command or trigger to read and print AmmoCounter value
    char command = Serial.read();
    if (command == 'R' || command == 'r') {
      byte savedMagSwEnable = readMagSwEnable();
      Serial.print("MagSwEnable Read: ");
      Serial.println(savedMagSwEnable);
      //Serial.print("MagSwEnable: ");
      //Serial.println(MagSwEnable);
      //Serial.print("EEPROM Write Count: ");
      //Serial.println(writeCount);
    }
  }


}
// ====================================================== End Main Loop ===========================================================


//---------------------------------------------------------------------------------------------------------------------------------
// this process butons after debounce, ie long and short clicks, and encoder value
void ProcessConsoleButtonManager()
{

  // Decode the rotary
  static unsigned long LastRotaryChange = 0;
  RotaryTurned = ROTARY_NONE;

  bool ConsoleRotaryAValue = (ConsoleRotaryAButtonState == BTN_ROSE) || (ConsoleRotaryAButtonState == BTN_HIGH);
  bool ConsoleRotaryBValue = (ConsoleRotaryBButtonState == BTN_ROSE) || (ConsoleRotaryBButtonState == BTN_HIGH);
  static bool LCAV = false;    //Last Console A Value
  static bool LCBV = false;   //Last Console B Value
  bool Change = false;

  if ( ConsoleRotaryAValue != LCAV )
  {
    Change = true;
  }

  if ( ConsoleRotaryBValue != LCBV )
  {
    Change = true;
  }

  if ( Change )
  {
    // RotaryTurned =, is the output of this bit
    if ( !ConsoleRotaryAValue && !ConsoleRotaryBValue )
    {
      if ( !LCAV && LCBV )
      {
        RotaryTurned = ROTARY_CW;
      }
      if ( LCAV && !LCBV )
      {
        RotaryTurned = ROTARY_CCW;
      }
    }

    LCAV = ConsoleRotaryAValue;
    LCBV = ConsoleRotaryBValue;
  }

  // ------- Handel Encoder speed control
  if  ((SystemMode == SYSTEM_MODE_NORMAL) && ( RotaryTurned == ROTARY_CCW ))
  {
   MotorSpeedFull += 5;
   if( MotorSpeedFull > 100 ) MotorSpeedFull = 100;
   //Serial.println ( MotorSpeedFull ); 
  }
  if  ((SystemMode == SYSTEM_MODE_NORMAL) && ( RotaryTurned == ROTARY_CW ))
  {
   MotorSpeedFull -= 5;
   if( MotorSpeedFull < 30 ) MotorSpeedFull = 30;
   //Serial.println ( MotorSpeedFull ); 
  }


  // ------------ Handle the Rotary Encoder button --------------------------------------
  static unsigned long LastConsoleRotaryDownTime = 0;
  static bool LastConsoleRotaryValue = false;
  Change = false;
  ConsoleRotaryButtonAction = BTN_ACTION_NONE;
  bool ConsoleRotaryValue = (ConsoleRotaryCButtonState == BTN_ROSE) || (ConsoleRotaryCButtonState == BTN_HIGH);
  if ( LastConsoleRotaryValue != ConsoleRotaryValue )
  {
    Change = true;
    LastConsoleRotaryValue = ConsoleRotaryValue;
  }
  if ( Change )
  {
    if ( !ConsoleRotaryValue )
    {
      if ( millis() - LastConsoleRotaryDownTime > BUTTON_PRESS_JUNK )
      {
        // Junk press.. Ignore
      }
      else if ( millis() - LastConsoleRotaryDownTime > BUTTON_PRESS_LONG )
      {
        ConsoleRotaryButtonAction = BTN_ACTION_LONG;
      }
      else if ( millis() - LastConsoleRotaryDownTime > BUTTON_PRESS_SHORT )
      {
        ConsoleRotaryButtonAction = BTN_ACTION_SHORT;
      }
    }
    if ( ConsoleRotaryValue )
    {
      LastConsoleRotaryDownTime = millis();
    }
  }

#ifndef EN_SEL_FIRE_SW                        //if we not defined selecfire then SF via Encoder PB
  // Execute Select Fire                                        
  if ( SystemMode == SYSTEM_MODE_NORMAL )
  {
    if ( ConsoleRotaryButtonAction == BTN_ACTION_SHORT )
    {
      SelectFireClk += 1;
      if ( SelectFireClk == 4)  SelectFireClk = 1;           //trap clicks 1-3 range

      if (SelectFireClk == 1) TargetFireMode = FIRE_MODE_SINGLE;

      if (SelectFireClk == 2) TargetFireMode = FIRE_MODE_BURST;

      if (SelectFireClk == 3) TargetFireMode = FIRE_MODE_AUTO;
    }
  }
#endif

  // ------------- Detect Long Trigger Press, Turns ideal mode on -------------
  static unsigned long LastTriggerDownTime = 0;
  static bool LastTriggerValue = false;
  bool TChange = false;
  TChange = false;
  TriggerButtonAction = BTN_ACTION_NONE;                      //reset the output
  bool TriggerValue = (TriggerButtonState == BTN_FELL) || (TriggerButtonState == BTN_LOW);
  if ( LastTriggerValue != TriggerValue )
  {
    TChange = true;
    LastTriggerValue = TriggerValue;
  }
  if ( TChange )
  {
    if ( !TriggerValue )
    {
      if ( millis() - LastTriggerDownTime > BUTTON_PRESS_JUNK )
      {
        // Junk press.. Ignore
      }
      else if ( millis() - LastTriggerDownTime > BUTTON_PRESS_LONG )
      {
        TriggerButtonAction = BTN_ACTION_LONG;
      }
      else if ( millis() - LastTriggerDownTime > BUTTON_PRESS_SHORT )
      {
        TriggerButtonAction = BTN_ACTION_SHORT;
      }
    }
    if ( TriggerValue )
    {
      LastTriggerDownTime = millis();
    }
  }
  
#ifndef EN_REV_SW                                // If EN_REV_SW is NOT defined - use long trigger press
  if ((TriggerButtonAction == BTN_ACTION_LONG) && (TargetFireMode == FIRE_MODE_SINGLE) && (IdleSpeed > 0))
  {
    if (IdleMode == false)                        // if off turn on
    {
      IdleMode = true;                            // set flag turn Idle on
      Serial.println ("Rev On");

      //IdleMotorSpeed = (IdleSpeed * 10) + 1000;
      //TargetMotorSpeed = IdleMotorSpeed;           // set new target speed
      MinMotorSpeed = (IdleSpeed * 10) + 1000;
      //MinMotorSpeedIdle = (IdleSpeed * 10) + 1000;
      TargetMotorSpeed = MinMotorSpeed;           // set new target speed
    

      //Serial.println ("IdleMotorSpeed");
      //Serial.println (IdleMotorSpeed);


    }
    else if (IdleMode == true)
    {
      IdleMode = false;                           // set flag idle off
      Serial.println ("Rev Off");
      MinMotorSpeed = 1000;
      TargetMotorSpeed = MinMotorSpeed;           // set new target speed
    }
    TriggerButtonAction = BTN_ACTION_NONE;
  }
#else
  //---- Rev switch to turn on/off ideal mode
  if ((RevSwButtonState == BTN_LOW ) &&  (IdleSpeed > 0) )      //turn idel on
  {
    if (IdleMode == false)                         // ifs off so turn on
    {
      IdleMode = true;                           // set flag turn Idle on
      MinMotorSpeed = (IdleSpeed * 10) + 1000;
      //MinMotorSpeedIdle = (IdleSpeed * 10) + 1000;
      TargetMotorSpeed = MinMotorSpeed;          // set new target speed
      SET_TRACER_D_ON;
    }
  }
  if ((RevSwButtonState == BTN_HIGH )  &&  (IdleMode == true))    //turn idel off
  {
    IdleMode = false;                           // set flag idle off
    MinMotorSpeed = 1000;
    TargetMotorSpeed = MinMotorSpeed;           // set new target speed
    digitalWrite( PIN_TRACER, LOW );
  }
#endif
}
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

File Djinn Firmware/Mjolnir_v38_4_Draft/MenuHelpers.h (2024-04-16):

// Menu object types
// Just chucked into a header because I don't want to have to have this at the top of the INO file :p

// This does range testing on the Config screen Values, Oled display

class MenuItem
{
  public:
  int CurrentValue = 0;
  char Title[8] = "\0";
  char Output[8] = "\0";

  virtual void Increase(  ) = 0;
  virtual void Decrease(  ) = 0; 
  virtual void PrepareOutput( ) = 0;
};

// ------------------------------------------------------------------------------
class GameTimeMenuItem : public MenuItem       // Game Timer Menu Item 1
{
  private:
    
    
  public:

  void Increase()
  {
    CurrentValue += 1;
    if( CurrentValue > 120 ) CurrentValue = 120;
  }
  void Decrease()
  {
    CurrentValue -= 1;
    if( CurrentValue < 0 ) CurrentValue = 0;   
  }
  void PrepareOutput()
  {
    sprintf( Output, "%4d", CurrentValue ); 
  }
};

// ------------------------------------------------------------------------------
class MotorMenuItem : public MenuItem       // Power Output Menu Item 2 & 3
{
  private:
    
    
  public:

  void Increase()
  {
    CurrentValue += 5;
    if( CurrentValue > 100 ) CurrentValue = 100;
  }
  void Decrease()
  {
    CurrentValue -= 5;
    if( CurrentValue < 30 ) CurrentValue = 30;   
  }
  void PrepareOutput()
  {
    sprintf( Output, "%3d%%", CurrentValue ); 
  }
};

// ----------------------------------------------------------------
class ROFMenuItem : public MenuItem         // ROF Menu Item 4 & 5 
{
  private:
    
    
  public:

  void Increase()
  {
    if( CurrentValue < 150 )
      CurrentValue += 10;
  }
  void Decrease()
  {
    if( CurrentValue > 0 )
      CurrentValue -= 10 ;
      
  }
  void PrepareOutput()
  {
    if( CurrentValue == 0 )
    {
      strcpy( Output, " MAX" );
    }
    else
    {
      sprintf( Output, "%4d", CurrentValue ); 
    }
  }
};

// --------------------------------------------------------------------------------
class BurstSizeMenuItem : public MenuItem     // Burst Size Menu Item 6
{
  private:
    
    
  public:

  void Increase()
  {
    if( CurrentValue < 49 )
      CurrentValue ++;
  }
  void Decrease()
  {
    if( CurrentValue > 1 )
      CurrentValue --;
  }
  void PrepareOutput()
  {
    sprintf( Output, "%4d", CurrentValue ); 
  }
};

// -------------------------------------------------------------------------
class MagSizeMenuItem : public MenuItem       // Mag Size Menu Item 7
{
  private:
    
    
  public:

  void Increase()
  {
    if( CurrentValue == 0 )
      CurrentValue = 6;
    else if( CurrentValue < 100 )
      CurrentValue ++;
  }
  void Decrease()
  {
    if( CurrentValue == 6 ) 
    {
      CurrentValue = 0;
    }
    else if( CurrentValue > 6 )
    {
      CurrentValue --;
    }
  }

  void PrepareOutput()
  {
    if( CurrentValue == 0 )  
    {
      strcpy( Output, "  UP" );
    }
    else
    {
      sprintf( Output, "%4d", CurrentValue );
    }
  }
};

// ----------------------------------------------------------------------------
class TimingMenuItem : public MenuItem                // Timing Menu Item 8-11
{
  private:
    
    
  public:

  void Increase()
  {
    CurrentValue += 50;
    if( CurrentValue > 5000 )
      CurrentValue = 5000;
  }
  void Decrease()
  {
    CurrentValue -= 50;
    if( CurrentValue < 0 )
      CurrentValue = 0;
  }
  void PrepareOutput()
  {
    sprintf( Output, "%4d", CurrentValue );
  }
};

// ----------------------------------------------------------------------------
class TimingMenuItemFine : public MenuItem                // Timing Menu Item for fine adjustment of Ramp Up 
{
  private:
    
    
  public:

  void Increase()
  {
    CurrentValue += 10;
    if( CurrentValue > 5000 )
      CurrentValue = 5000;
  }
  void Decrease()
  {
    CurrentValue -= 10;
    if( CurrentValue < 0 )
      CurrentValue = 0;
  }
  void PrepareOutput()
  {
    sprintf( Output, "%4d", CurrentValue );
  }
};

//-------------------------------------------------------------------------------------------
class SolenoidTimingMenuItem : public MenuItem       //Solenoide Timing Menu Items 12, 13, 14
{
  private:
    
    
  public:

  void Increase()
  {
    if( CurrentValue == 0 )
      CurrentValue = 1;
    else if( CurrentValue < 1000 )
      CurrentValue ++;
  }
  void Decrease()
  {
    if( CurrentValue == 0 ) 
    {
      CurrentValue = 0;
    }
    else if( CurrentValue > 0 )
    {
      CurrentValue --;
    }
  }

  void PrepareOutput()
  {
    if( CurrentValue == 0 )  
    {
      strcpy( Output, "  UP" );
    }
    else
    {
      sprintf( Output, "%4d", CurrentValue );
    }
  }
};

// --------------------------------------------------------------------------------
class BatteryMenuItem : public MenuItem     //Battery type, Menu Item 15
{
  private:
    
    
  public:

  void Increase()
  {
    CurrentValue ++;
    if( CurrentValue > 4 )
      CurrentValue = 4;
  }
  void Decrease()
  {
    CurrentValue --;
    if( CurrentValue < 3 )
      CurrentValue = 3;
  }
  
   void PrepareOutput()
  {
    if( CurrentValue == 3 )
    {
      strcpy( Output, "  3S" );
    }
    if ( CurrentValue == 4 )
    {
      strcpy( Output, "  4S" ); 
    }
  }
};

// --------------------------------------------------------------------------------
class IdleSpeedMenuItem : public MenuItem                //Idle Speed  Menu Item 16
{
  private:
    
    
  public:

  void Increase()
  {
    if( CurrentValue == 100 )
      CurrentValue = 100;
    else if( CurrentValue < 100 )
      CurrentValue += 5;
  }
  void Decrease()
  {
    if( CurrentValue == 0 ) 
    {
      CurrentValue = 0;
    }
    else if( CurrentValue > 0 )
    {
      CurrentValue -= 5;
    }
  }

  void PrepareOutput()
  { 
      sprintf( Output, "%4d", CurrentValue );
  }
};

// --------------------------------------------------------------------------------
class ROF_RampTimeMenuItem : public MenuItem     //ROF RAMP Time on Auto, Menu Item 17
{
  private:
    
    
  public:
  
  void Increase()
  {
    if( CurrentValue == 0 )
      CurrentValue = 1;
    else if( CurrentValue < 1000 )
      CurrentValue ++;
  }
  void Decrease()
  {
    if( CurrentValue == 0 ) 
    {
      CurrentValue = 0;
    }
    else if( CurrentValue > 0 )
    {
      CurrentValue --;
    }
  }

  void PrepareOutput()
  { 
      sprintf( Output, "%4d", CurrentValue );
  }
};

// --------------------------------------------------------------------------------
class MagSwEnableMenuItem : public MenuItem     //AmmoCounterMenuItem, linked to 
{
  private:
    
    
  public:

  void Increase()
  {
    CurrentValue ++;
    if( CurrentValue > 1 )
      CurrentValue = 1;
  }
  void Decrease()
  {
    CurrentValue --;
    if( CurrentValue < 1 )
      CurrentValue = 0;
  }
  
   void PrepareOutput()
  {
    if( CurrentValue == 0 )
    {
      strcpy( Output, "  OFF" );
    }
    if ( CurrentValue == 1 )
    {
      strcpy( Output, "  ON" ); 
    }
  }

};
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
